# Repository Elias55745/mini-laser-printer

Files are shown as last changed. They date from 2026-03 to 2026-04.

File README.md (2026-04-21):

# mini-laser-printer
My store, http://www.makerstore.fun, offers both finished products and DIY kits. We help you save time and money by sourcing parts for you.
If you prefer to source them yourself, you can shop on platforms like AliExpress or Amazon, though the total cost may be higher. If you choose this option, please purchase the following items in order:
| Item Name | Specs/Parameters | Qty | Recommendations & Tips |
| :--- | :--- | :---: | :--- |
| Custom Motherboard (PCB) | Integrated Large & Small Board | 1 Set | Includes both boards. |
| NANO Development Board | - | 1 | Must select Mini USB interface version. |
| A4988 Stepper Driver | - | 2 | Recommended to keep one as a spare. |
| FPC Flexible Cable | 10cm, 1.0mm-4P | 1 | Critical Spec: Reverse/Flip connector. |
| Data Cable | Matching Interface | 1 | Must match the dev board (usually Mini USB). |
| Laser Head | 5V 250mW | 1 | For wood/leather/paper. Dark objects work best. Cannot engrave metal. |
| Case Printed Parts | PLA/PETG | 1 Set | - |
| Screws | M2.5 * 8 Countersunk | 17 | For fixing frame and circuit board. |
| Screws | M2 * 4 Countersunk | 8 | For fixing motor bracket and adapter board. |
| Micro Stepper Motor | 58mm screw rod, 3mm pitch | 3 | Recommend Samsung ODD salvage motors (longer stroke, cost-effective). |
| Cooling Fan | 5010 Blower, 5V | 1 | Check holes: Recommend 4-hole mount. Common 3-hole fans need modification. |
| Optical Shaft (Rod) | Diameter 3mm | 4 | Lengths: 100mm (2 pcs) and 82mm (2 pcs). Search "dowel pins" or custom. |
| Grease | - | 1 | Apply to optical rods and screw rods. |
| Power Supply | 12V/9V 2A | 1 | Interface DC5.5*2.1. Do not exceed 12V (On-board components rated 16V). |
| Light Shield | Green Translucent Plastic | 1 | Recommend Green Cellophane/PVC (not sticker). Filters red light. |
| Safety Goggles | Green | 1 | Must wear! Darker is better. Never look directly at the laser. |

Download the circuit files from the repository and choose a cost-effective PCB manufacturer to fabricate the board. Below is the list of required components:
| Item Name | Specs / Parameters | Qty |
| :--- | :--- | :---: |
| FPC Connector | 4P-1mm, Bottom-contact Flip-lock | 2 |
| | 4P-1mm, Top-contact Drawer | 3 |
| XH2.54 Terminal | 2P, Horizontal | 1 |
| PH2.0-2P | 2P, Horizontal | 1 |
| DC044 Power Jack | DC044 Plastic Shell | 1 |
| 2.54mm Single Row Female Header | 1*15P | 2 |
| | 1*8P | 4 |
| SMD Aluminum Electrolytic Capacitor | 16V 220UF, 6.3*7.7mm | 4 |
| 1206 SMD Capacitor | 0.1UF | 3 |
| 1206 SMD Resistor | 10Ω | 1 |
| | 10K | 4 |
| MOSFET | 30N3P | 1 |
| Power Regulator | XL1509-5.0 | 1 |
| Power Inductor | 68UH | 1 |
| Diode | SS34, SMA Package | 1 |

When using this printer, please pay attention to electrical safety and use the provided protective goggles!

If you purchase the finished product, no firmware flashing is required. For the DIY kit, please upload the program to the Nano board.To make changes, modify the code in the repository and re-flash the ATmega328 main controller. If you don't need to customize the firmware, simply ignore this notice.

#User Guide

1.If this is your first time using the device, please open the repository, access the motherboard driver folder, and install the CH341SER driver.

2.After installing the motherboard drivers, please run the host software installer. Once completed, select LaserGRBL to install the control software for this laser printer. Finally, select the COM port connected to your computer from the left panel and click Connect. All configuration is now complete.

Assembly Instructions: 
First, install the motor as shown in the figure and tighten the screws.
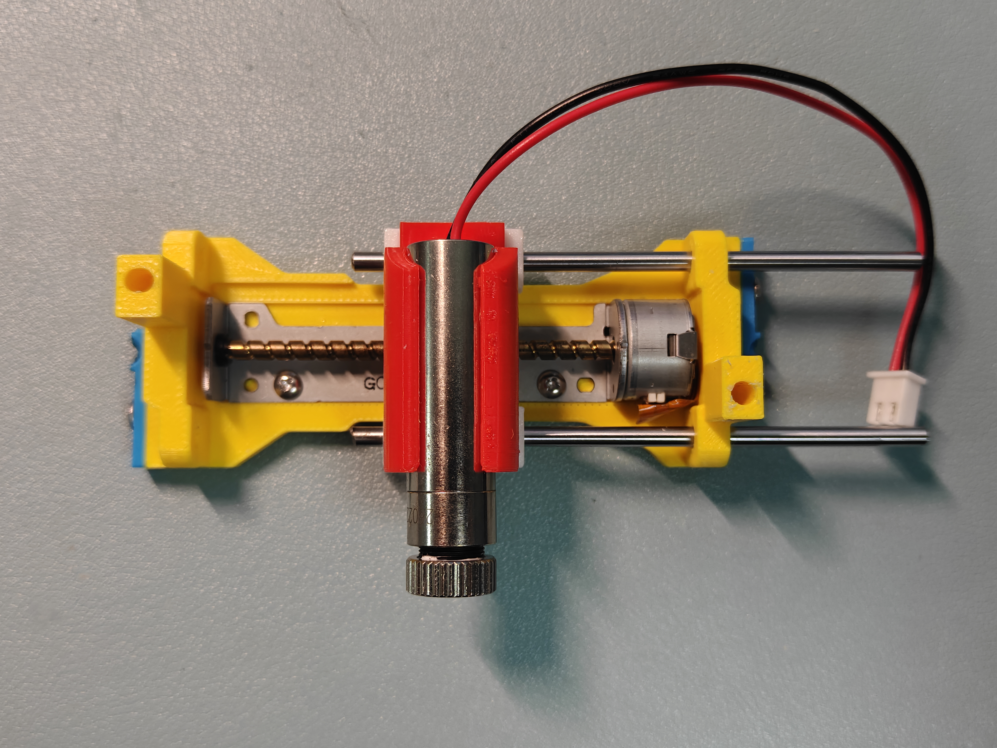
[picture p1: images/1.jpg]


Take two short shafts and insert them halfway as shown in the figure. Install the laser head into the fixture, insert the short shafts, and finally push the shafts all the way into the bottom.
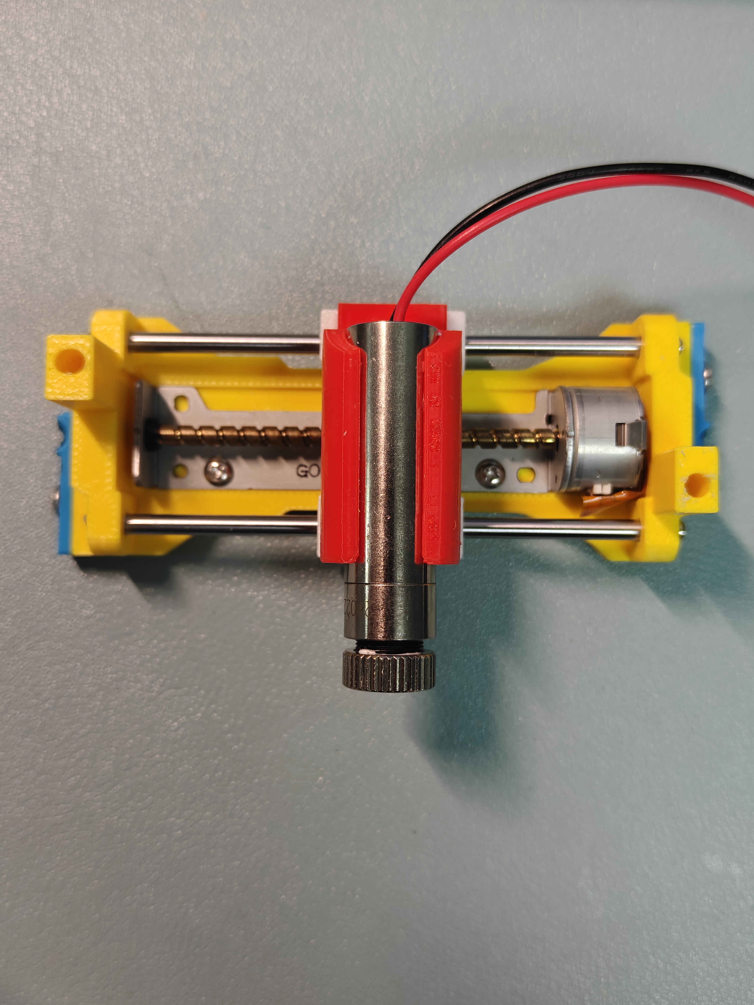
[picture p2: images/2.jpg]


Assemble the two stepper motors as shown.


Assemble the turbofan as shown.
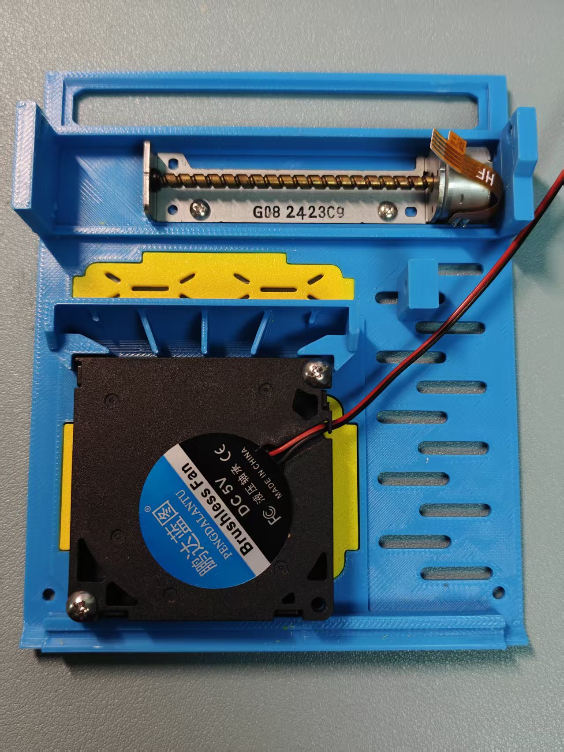
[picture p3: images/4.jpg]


Take out the mainboard, use pliers to snap off the small board as shown, and then screw it onto the back of the laser slide rail.Warning: Please ensure the stepper motor driver board is oriented as shown in the figure. Incorrect installation may cause damage to the board.
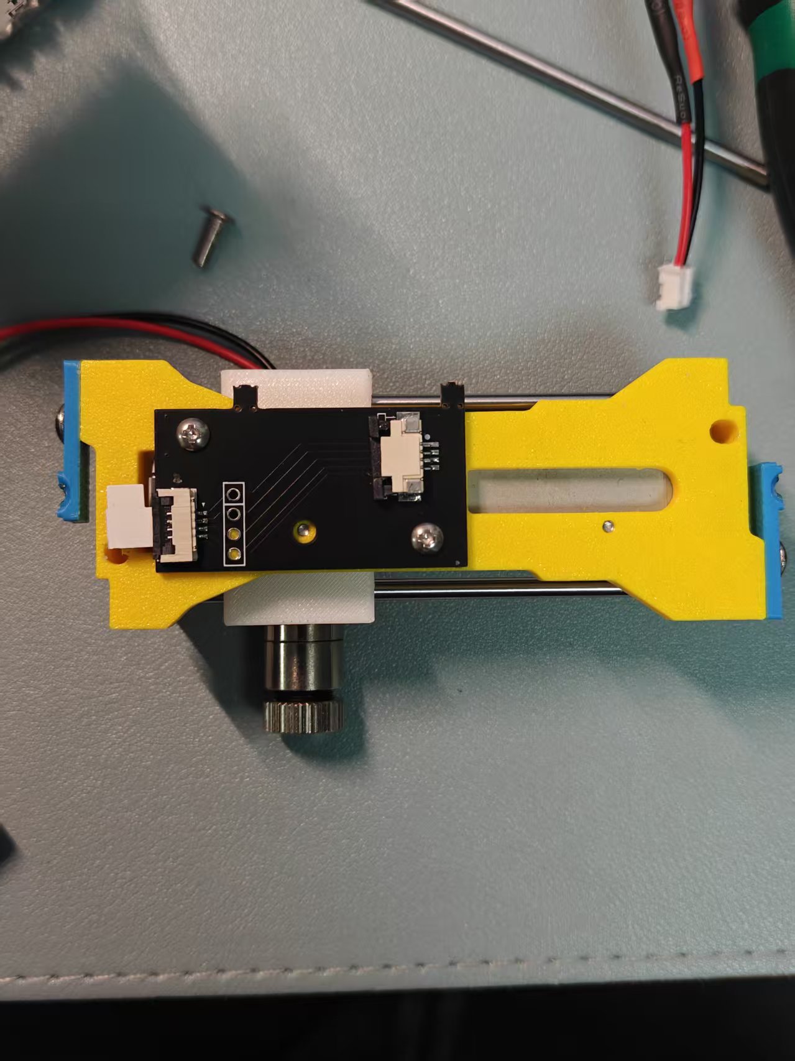
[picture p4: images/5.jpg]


Then, connect the stepper motor flat cable to the small board.
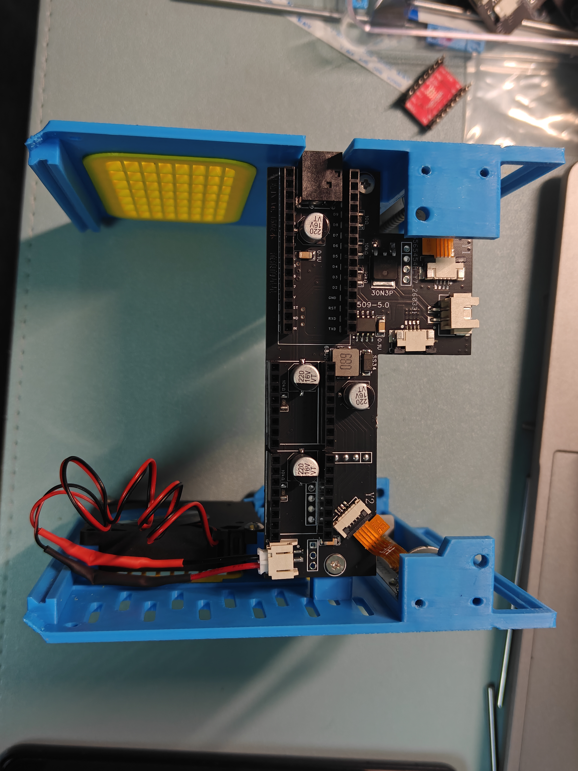
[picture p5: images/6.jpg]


Secure the mainboard to the mounting holes.
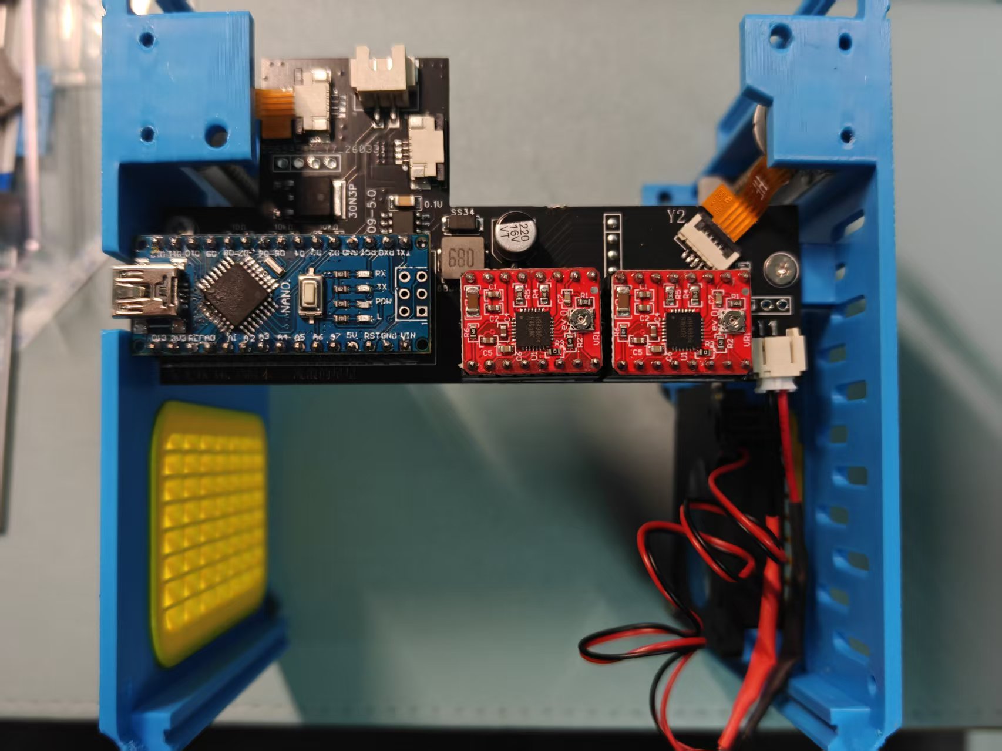
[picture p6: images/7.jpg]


Take out the long shaft and insert the laser slide rail into the main body.
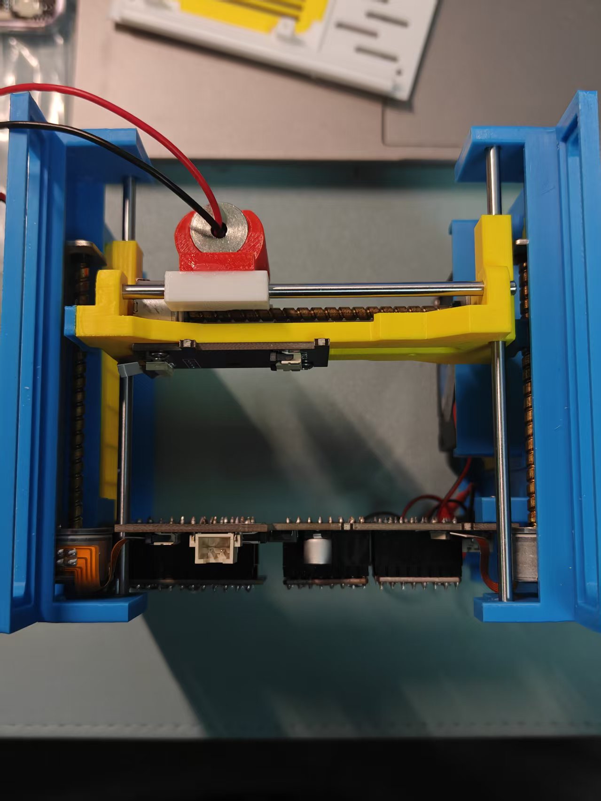
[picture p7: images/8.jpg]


Connect the laser power supply and the flat cable.
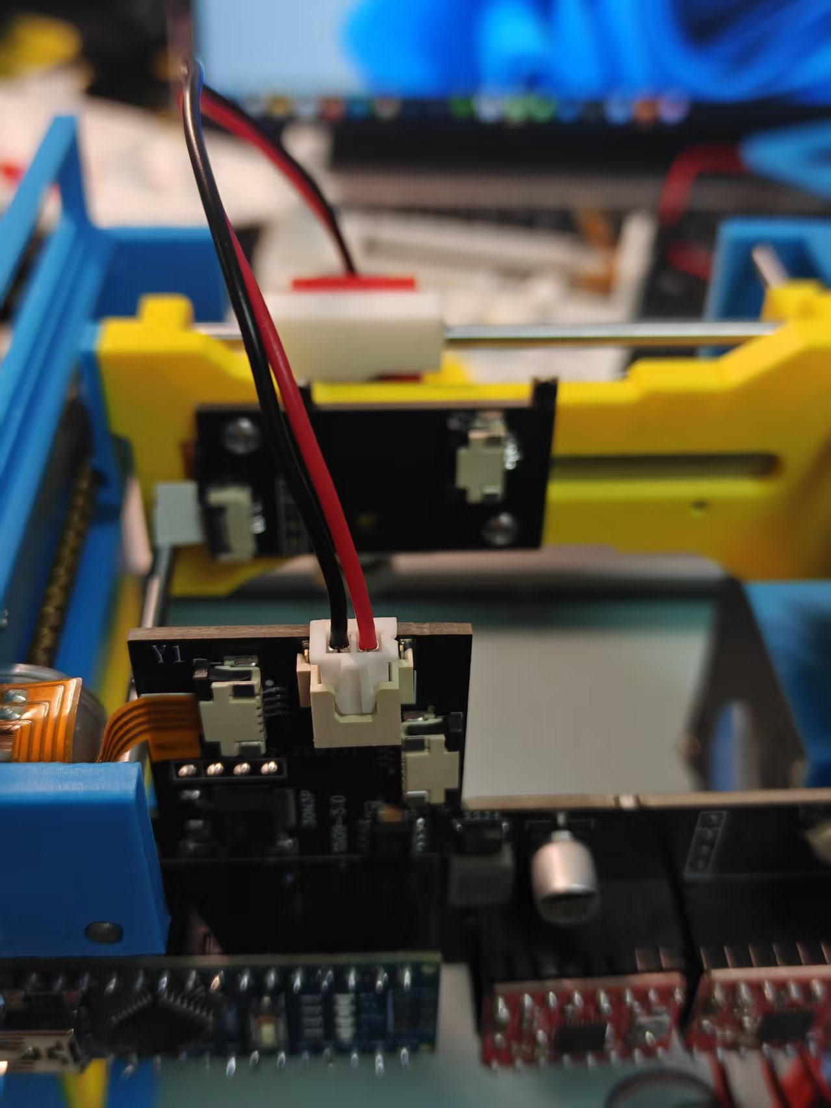
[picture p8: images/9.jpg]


Finally, install the remaining parts and tighten the screws.

Note: For this drawer-style FPC connector, the metal contacts on the flat cable must face upwards when inserted.
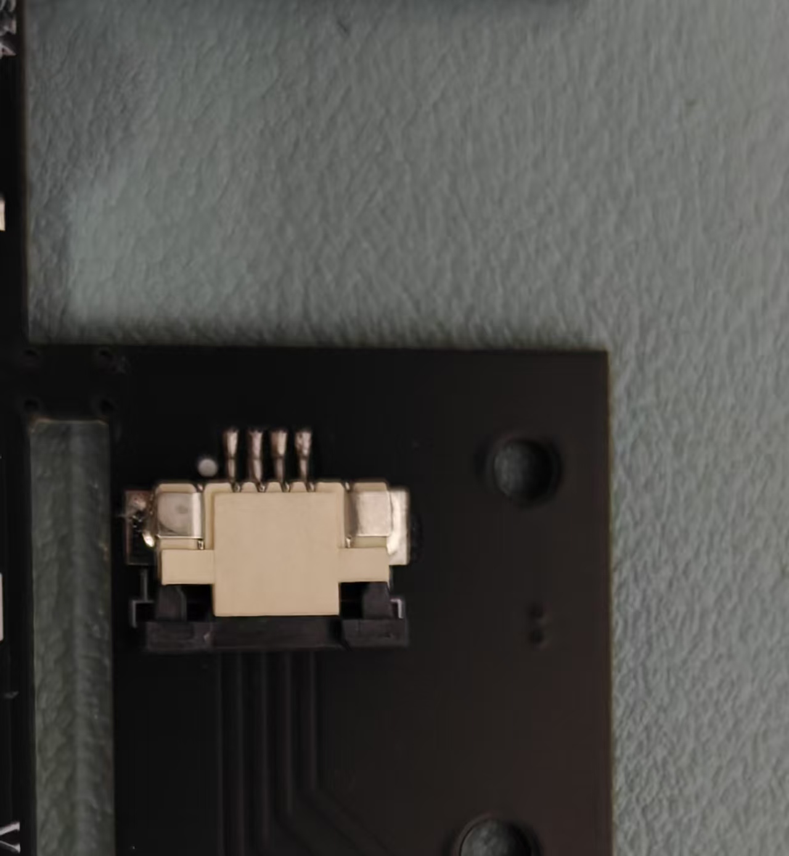
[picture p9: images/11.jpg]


For this clamshell FPC connector, the metal contacts on the flat cable must face downwards when inserted.
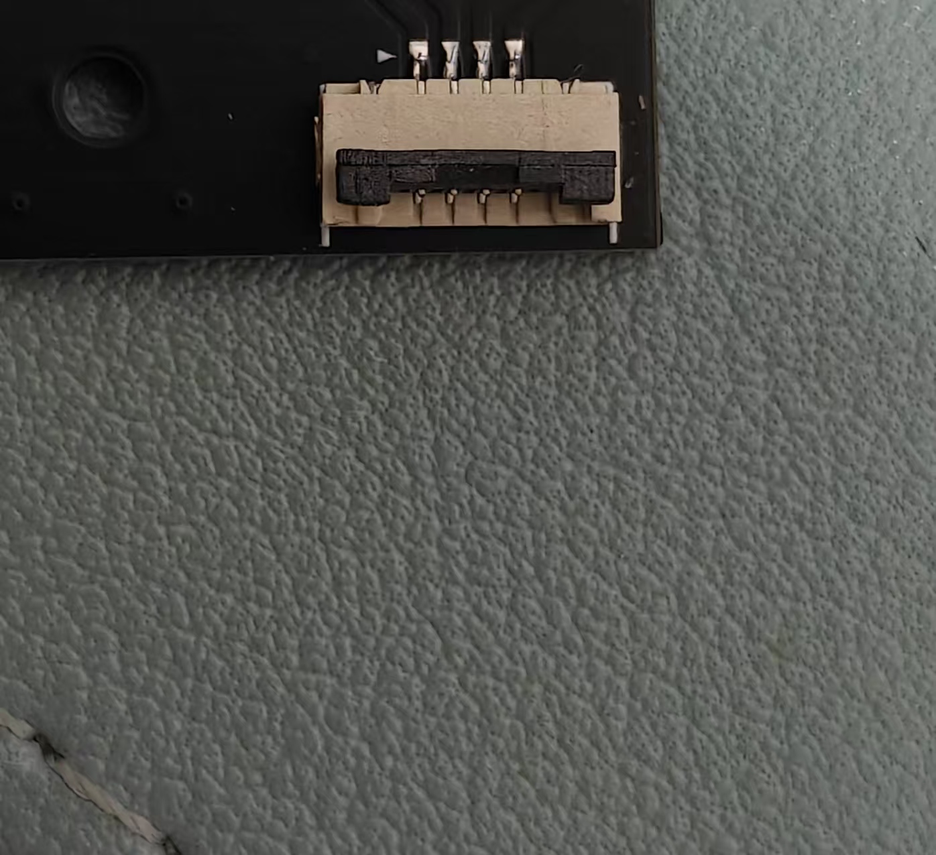
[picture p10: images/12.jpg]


Debugging:
Connect the 12V power supply. Connect one probe of the multimeter to the metal shell of the USB port on the Nano board, and connect the other probe to the potentiometer of the stepper motor driver as shown in the figure.
Check the voltage and use a small flat-head screwdriver to adjust the left stepper motor driver to 0.28V and the right one to 0.5V.
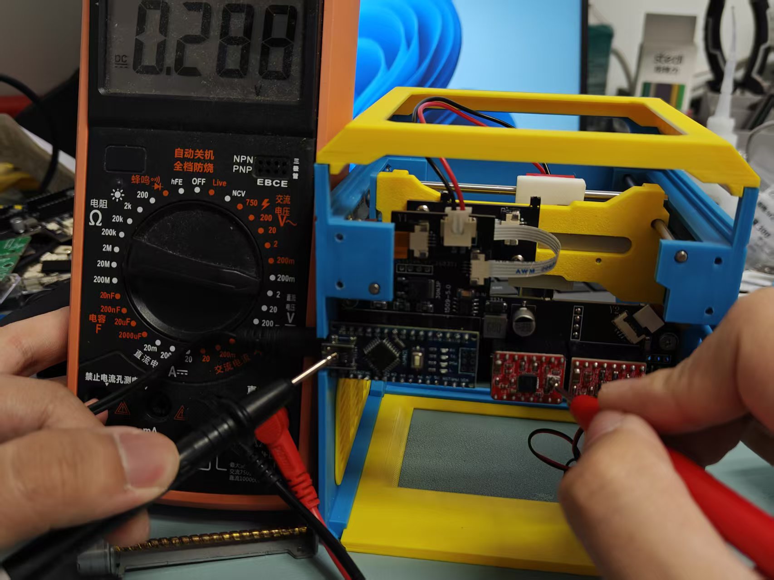
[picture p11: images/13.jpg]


The laser module in the kit requires focusing. You need to adjust it until the laser beam converges to the smallest possible point.

If the sliding is not smooth, fine-tuning of the various structural components may be required.

Connect the power supply to the printer and the USB cable to the computer. Download the LaserGRBL host software from the repository. As shown in the figure, select the printer's COM port, set the baud rate to 115200, and click the green button to connect.
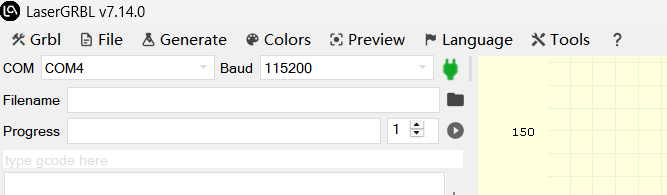
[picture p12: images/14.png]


Next, click on "Grbl" in the menu bar and select "Grbl Configuration". Import the two files with the .nc extension from the LaserGRBL folder in the GitHub repository. Finally, click "Refresh" and then close the window.
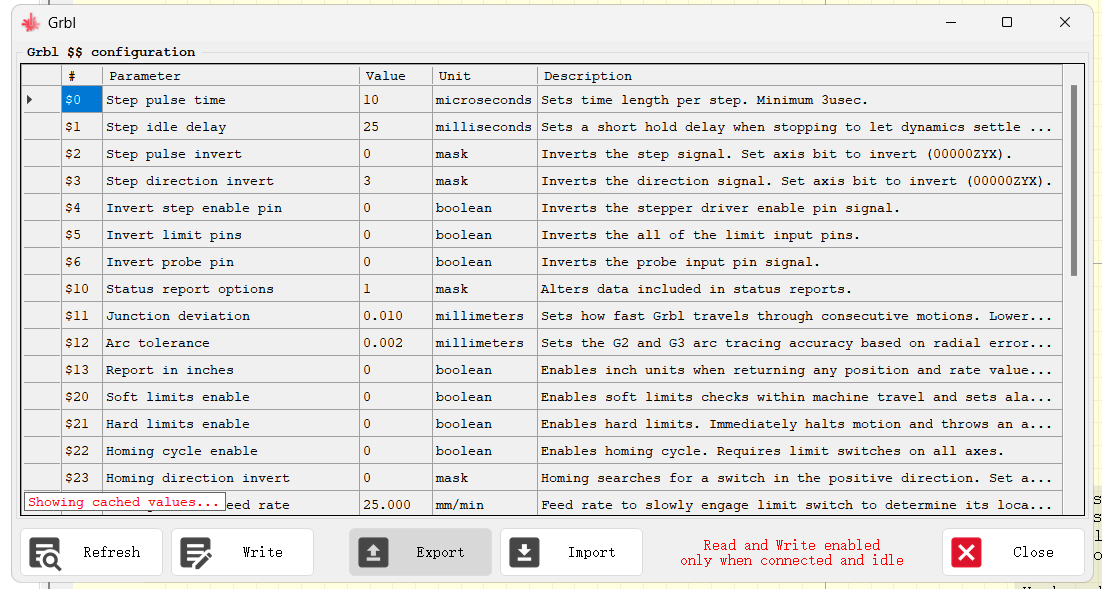
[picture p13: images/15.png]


Click "File" to select the image you want to print. You can choose the conversion method, and then adjust parameters like printing speed to improve the print quality.

Increasing the quality setting appropriately can improve the print result; similarly, lowering the printing speed works too.
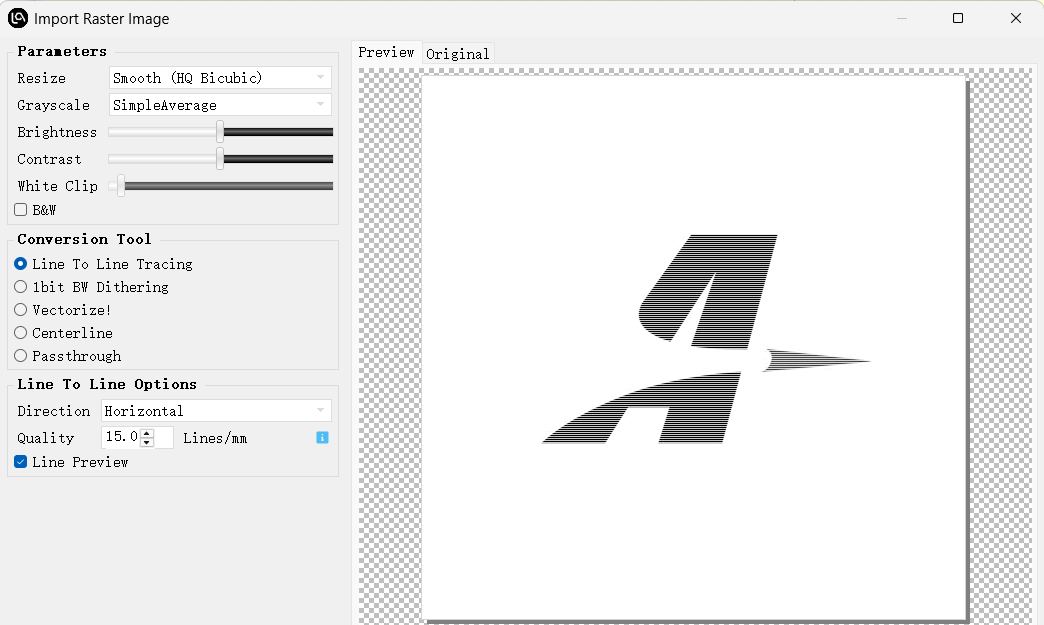
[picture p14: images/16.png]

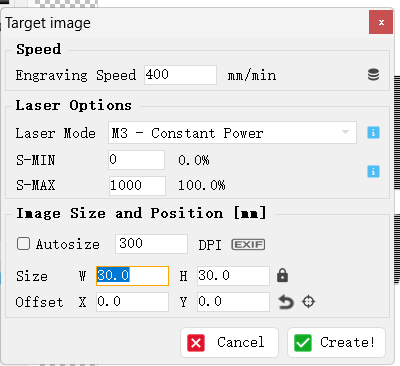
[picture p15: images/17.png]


For printing, it is recommended to choose dark-colored objects. This ensures that the energy is absorbed rather than reflected.

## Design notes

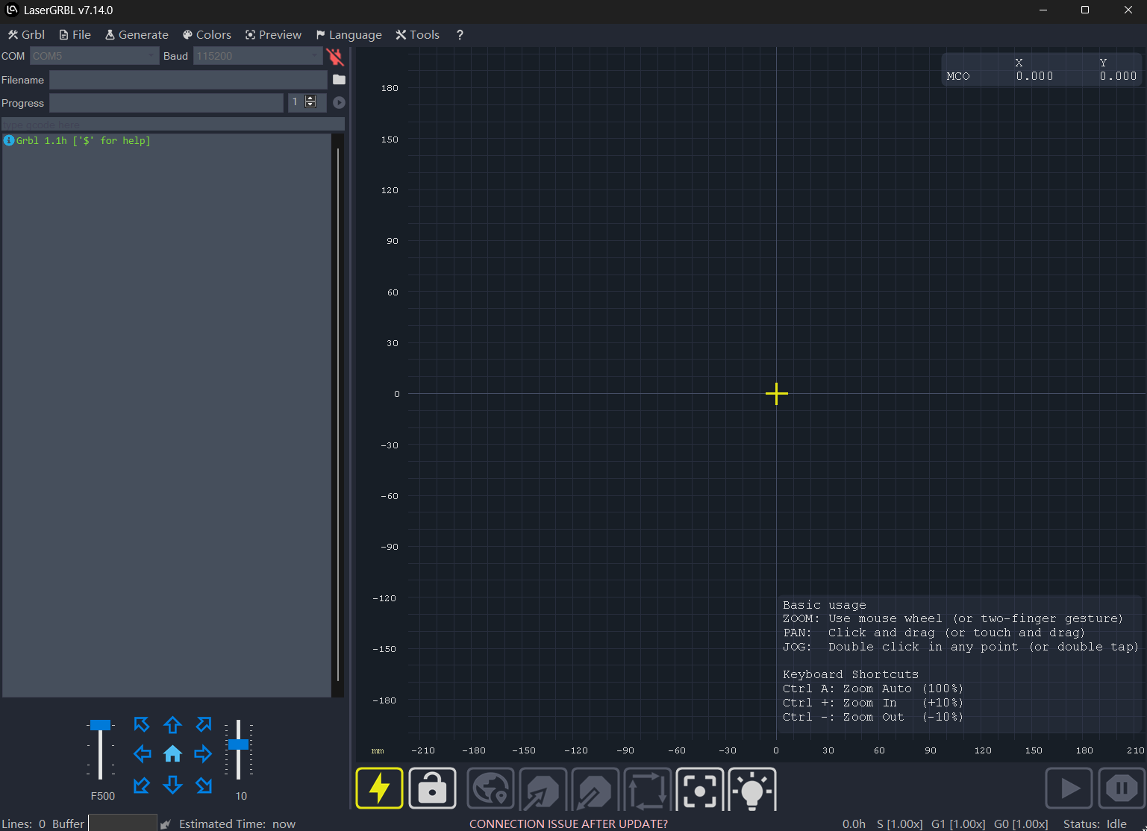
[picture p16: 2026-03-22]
lasergrbl1.png

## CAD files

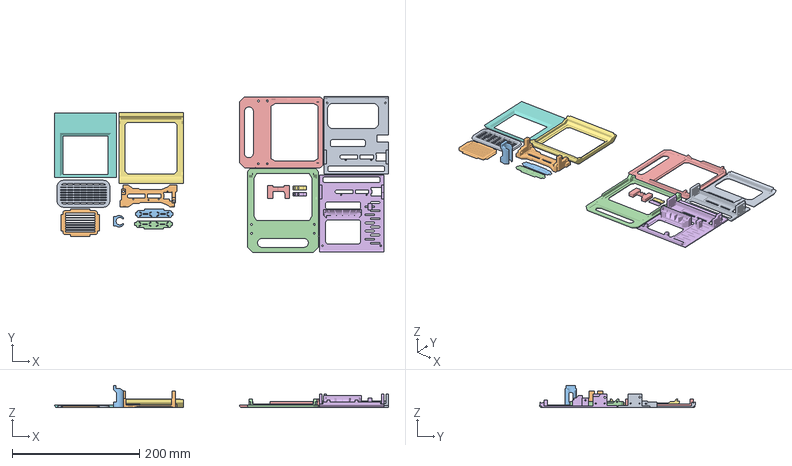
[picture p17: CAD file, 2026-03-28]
Case Printed Parts.3mf
526.0 x 245.4 x 35.0 mm
星光4N6.45版本stl.stl_14
星光4N6.45版本stl.stl_13
星光4N6.45版本stl.stl_5
星光4N6.45版本stl.stl_1
星光4N6.45版本stl.stl_4
星光4N6.45版本stl.stl_15
星光4N6.45版本stl.stl_2
星光4N6.45版本stl.stl_6
星光4N6.45版本stl.stl_7
星光4N6.45版本stl.stl_9
星光4N6.45版本stl.stl_3
星光4N6.45版本stl.stl_10
星光4N6.45版本stl.stl_8
星光4N6.45版本stl.stl_11
星光4N6.45版本stl.stl_12
